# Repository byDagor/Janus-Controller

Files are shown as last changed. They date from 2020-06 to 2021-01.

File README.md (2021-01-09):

# Janus Controller 20.01

The Janus Controller is a Brushless motor driver with an on-board magnetic encoder, a three-phase MOSFET driver, three MOSFET half-bridges, a temperature sensor and current sensing resistors. 

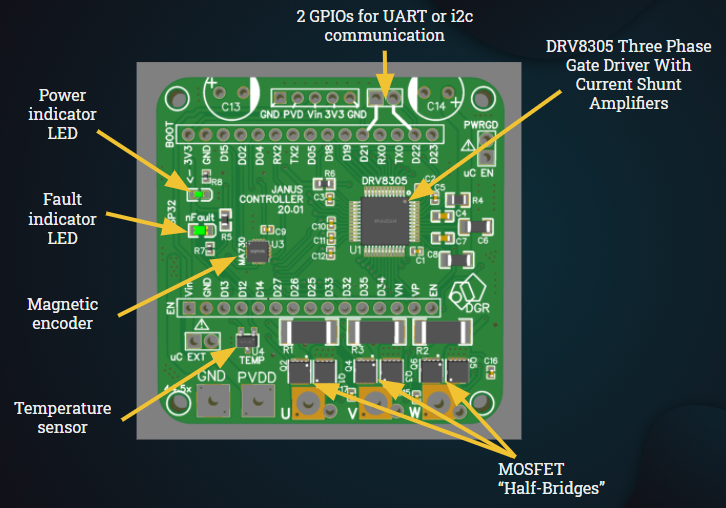
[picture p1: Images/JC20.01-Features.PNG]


Janus Controller was designed to work with the ESP32 Dev-Kit1 as a shield so that the programing of the board is easier for hobbyist and students, and to bring down the overall price of the board.
This board can be used to drive brushless motors as an open-loop system or use the on-board encoder to drive the motors as a closed-loop system and use more complicated algorithms, such as Field Oriented Control for position and velocity control.
I recommend using the [Simple FOC](https://github.com/askuric/Arduino-FOC) Arduino library as it has shown to work perfectly for position and velocity control and is easily implementable, but you can always use your own algorithm. My [example code](JC01F05/JC01F05.ino) uses the [Simple FOC](https://github.com/askuric/Arduino-FOC) library adapted to work with an ESP32.

## Key specs
| Specification | Rating |
| --- |:---:|
| Dimensions | 51 x 51mm |
| Power source voltage | 5-12V |
| Maximum continuous current | Depends on cooling |
| Maximum peak current  | up to 23A |
| Encoder resolution | 4096 cpr/ 0.088 degrees |
| Temperature sensor range | -10 ~ 120°C |

## Getting started

### The board
In this repository you can find everything you need to get you started with your personal projects. The board was designed around the [JLCPCB SMT Parts Library](https://jlcpcb.com/parts), so you should be able to order an SMD assembled board directly from them for a low price. 
You can order this board from your preferred manufacturer, you just need to download the [gerber files](Gerber) and the [SMD BOM](BOM_JC20.01.csv). If you don't order your board from JLCPCB you should make sure that the manufacturer has in stock the needed SMD parts, if not it shouldn't be too difficult to find a replacement (except for the DRV8305 and the MA730).
Furthermore, if you wish to design your own board the [schematic](Schematic) can be a great place to start.  

After receiving the SMD assembled board you need to solder two 470 uF electrolytic capacitors, a few male/ female pins and a voltage source connector. The pins and the connector are optional, but I highly recommend using female header pins for the ESP32 Dev-kit.
The video bellow shows what is needed to prepare the board and how to do it. Alternatively, you can find the needed components in the [*though-hole* BOM](BOM).
<a href="http://www.youtube.com/watch?feature=player_embedded&v=tti3y8_cQ4o
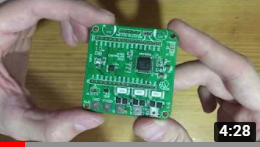
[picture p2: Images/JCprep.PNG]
IMAGE ALT TEXT HERE
" target="_blank"></a>

### ESP32 DEVKIT
As stated before, the Janus Controller was designed as a *shield* for the ESP32 DEVKIT V1. There are a few different ESP32 Devkits out there, make sure the one you buy has the same PIN layout as the Janus Controller.

## Set-up

### The three-phase gate driver
The DRV8305 is a three-phase gate driver that can drive high and low-side N-channel MOSFETS. What makes this driver special is the bunch of programable functions and the protection included.
With the Janus Controller you can use the DRV8305 in its three operation modes: 6-PWM input, 3-PWM input or 1-PWM input. The [example code](JC01F05/JC01F05.ino) works with the driver set through SPI to operate in the 3-PWM mode.
One feature I like is its fault diagnostics, if the nFault pin pulses it means there is a *warning* that can be read through SPI. If the pin is pulled low it means the driver detected a *fault*, which can also be read through SPI, and the output MOSFETs will be placed in their high impedance state.
The Janus Controller board has a red indicator LED that will turn on if a *warning* or a *fault* is detected.
A few of the faults that the driver reports are the following: high temperature flags, source under or over-voltage, VDS over current monitors, gate drive fault, etc.
The picture bellow shows the simplified schematic of the driver that can be found in the [DRV8305 datasheet](https://www.ti.com/lit/ds/symlink/drv8305.pdf?ts=1593641896221&ref_url=https%253A%252F%252Fwww.google.com%252F). Please refer to it if you want to learn more about all the features of this driver IC.
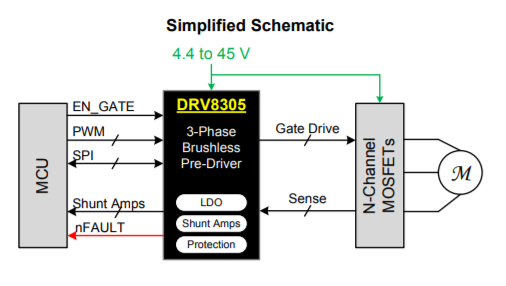
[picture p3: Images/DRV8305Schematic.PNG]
DRV8305
 

### The on-board encoder
The MA730 Magnetic Encoder works with a diametrically polarized magnet, these can be hard to find but you should be able to find a couple options from eBay. 
The [MA730 datasheet](https://www.monolithicpower.com/en/documentview/productdocument/index/version/2/document_type/Datasheet/lang/en/sku/MA730/document_id/3563) recommends a Neodymium alloy (N35) cylinder with dimensions Ø5x3mm inserted into an aluminum shaft, as shown in the picture bellow, placed around 1.5mm above the encoder IC. 
You can use a solid cylindrical magnet of different dimensions without the aluminum shaft and still get excellent results.  

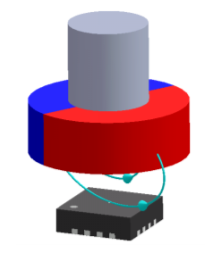
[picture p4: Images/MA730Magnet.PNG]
Magnet
   
The Janus Controller can read the 12-bit ABZ quadrature pins of the encoder to find the position of the rotor. Additionally, a PWM signal can be read to find the absolute position of the rotor (this hasn't been implemented in example code at the moment). 

### External encoder
If you don't want to use the on-board encoder, Janus Controller has access to two GPIOs of the ESP32. These pins can be used to use an external quadrature encoder that should be conected as shown in the picture. Read your encoder's datasheet and check if it needs pull-ups, if so you should be able to use the ESP32's internal pull-ups.
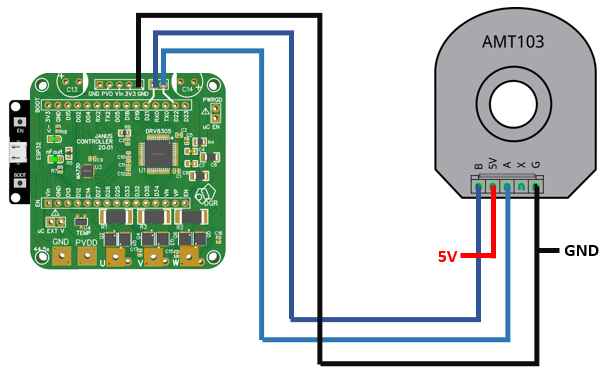
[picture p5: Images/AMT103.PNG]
External encoder


## The example code
The example code was done in the Arduino IDE, running the [Simple FOC](https://github.com/askuric/Arduino-FOC) Arduino Library. By changing a simple parameter, this code allows you to control position and velocity of your burshless motor, or setting a voltage as you would do with a DC motor. 
Make sure you follow the following steps to make sure the code will compile.

### 1. ESP32 set-up
*Random nerd tutorials* have a really easy to follow guide on how to set-up the ESP32 on the Arduino IDE. Follow the steps on [this link](https://randomnerdtutorials.com/installing-the-esp32-board-in-arduino-ide-windows-instructions/) and make sure you can compile one of the examples shown.

### 2. Running the encoder example
Download the [Encoder Tester](JC01F05/JC01F05.ino) and open it on your Arduino IDE. Upload it to the ESP32 and open the Serial terminal and make sure the measurement is accurate. Move the motor's rotor one whole whole rotation and make sure the trerminal prints 360 degrees. 

### 3. Simple FOC library installation
The [Simple FOC](https://github.com/askuric/Arduino-FOC) repository has an extremely detailed explanation on how to install the library. The easiest way is to install it through the library manager as shown in the picture.  
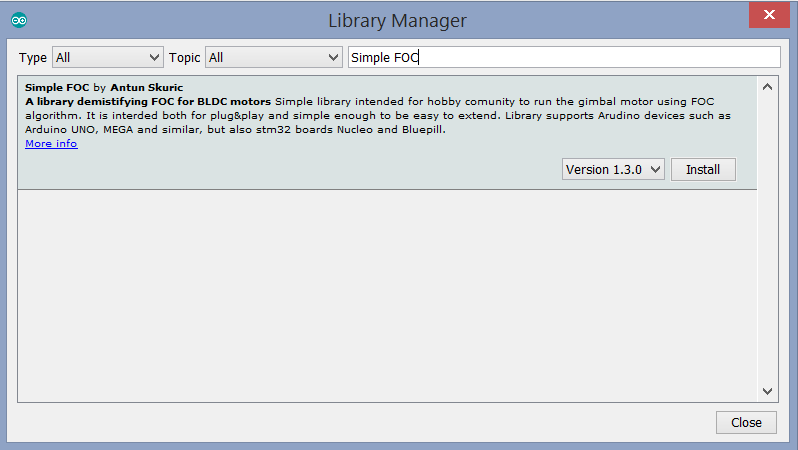
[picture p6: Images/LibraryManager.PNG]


### 4. Running the position control example
Download the [position control example code](JC01F05/JC01F05.ino) and open it on your Arduino IDE; there are a few parameters that you might have to tweak. I really recommend reading the [Simple FOC](https://github.com/askuric/Arduino-FOC) documentation. 

## Brushless motor selection
There are a few general rules that should help you choose the best brushless motor for your particular application. For instance, if you want to build a robot arm, a gimbal, or something that needs relative high torque you should get a low KV motor (usually bellow 300 is good) with a big radius in relation to its length. 
Usually, outrunner brushless motors have more poles than their counterpart, the inrunner, so they spin slower and produce more torque. This makes an outrunner the better choice for this type of application. 
We can use the torque equation of a brushless motor to calculate the ideal torque a motor will produce at a given voltage/ current. The value calculated with this formula will not be the real value because motors are far from ideal. I've found that considering a motor efficiency of around 80% should be good enough for estimating the maximum torque of a brushless motor.
TorqueFormula  \
If you're not sure how much current the motor will draw you can substitute de current in the formula for voltage over the internal resistance of the motor, as show in the equation (2). 
If the internal resistance of the motor seems too low, there is a parameter in the [example code](JC01F05/JC01F05.ino) that restricts the voltage applied to the motor. Generally, a resistance of around 10 ohms should be perfect.  
TorqueFormula2  

## Test Station
The test station is a 3D printed base that holds together the Janus Controller board and a brushless motor with a diametrically polarized magnet. This magnet is attached to the rotor of the motor and placed above the magnetic encoder; around 1.5mm above the encoder is optimal, making sure the center of the magnet is aligned with the center of the encoder.
In the [CAD](CAD) section you can find the CAD for the Test Station, the Janus Controller board, the motor used, the magnet used and the ESP32 Dev-kit. The CAD of the Janus Controller should help you design your own fixture to hold the board near your motor. 

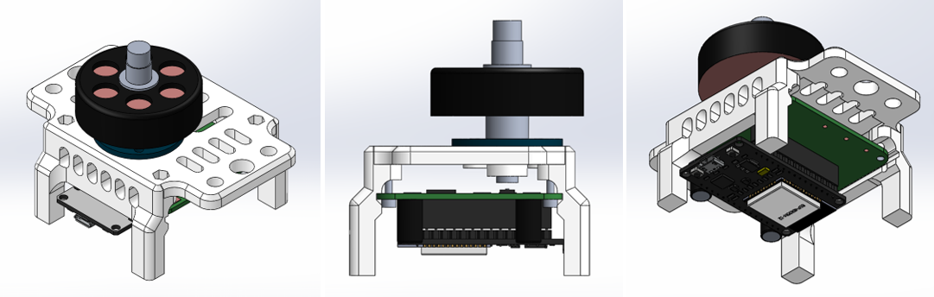
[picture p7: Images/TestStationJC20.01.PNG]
TestStation


## Practical Example
Big J is a five-bar parallel robot that uses direct drive brushless motors as actuators working with two Janus Controllers in position control mode and a master ESP32. Click the image bellow to watch a demo YouTube video.

<a href="http://www.youtube.com/watch?feature=player_embedded&v=JJa_QzbcREA
" target="_blank">IMAGE ALT TEXT HERE</a>

## Contact
I'm happy to hear from your projects and to help in any way possible!  
davidglzrys@gmail.com  
[Linkedin](https://www.linkedin.com/in/david-g-reyes/)  
[YouTube](https://www.youtube.com/channel/UC4gsPZan2T4v5LpJ5J_t7sQ/featured)

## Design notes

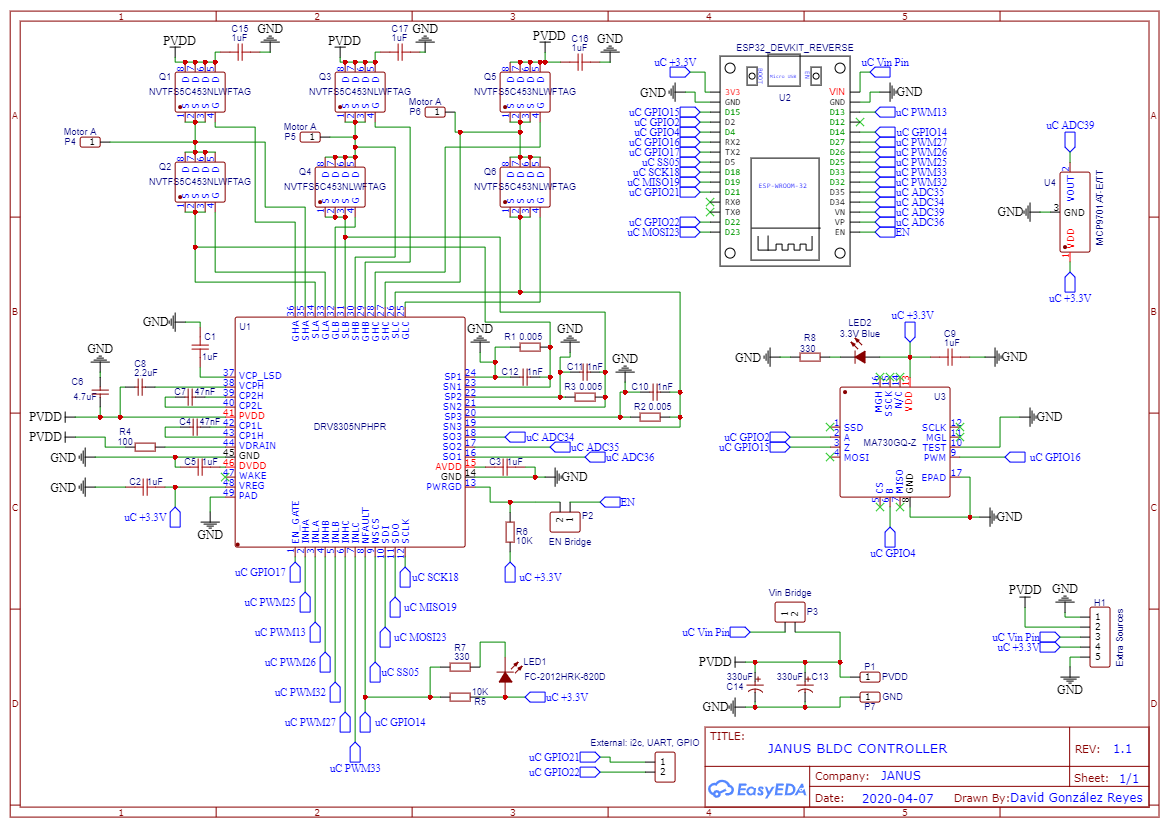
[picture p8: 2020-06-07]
JC20.01/Schematics/JanusController20.01_Schematics.png

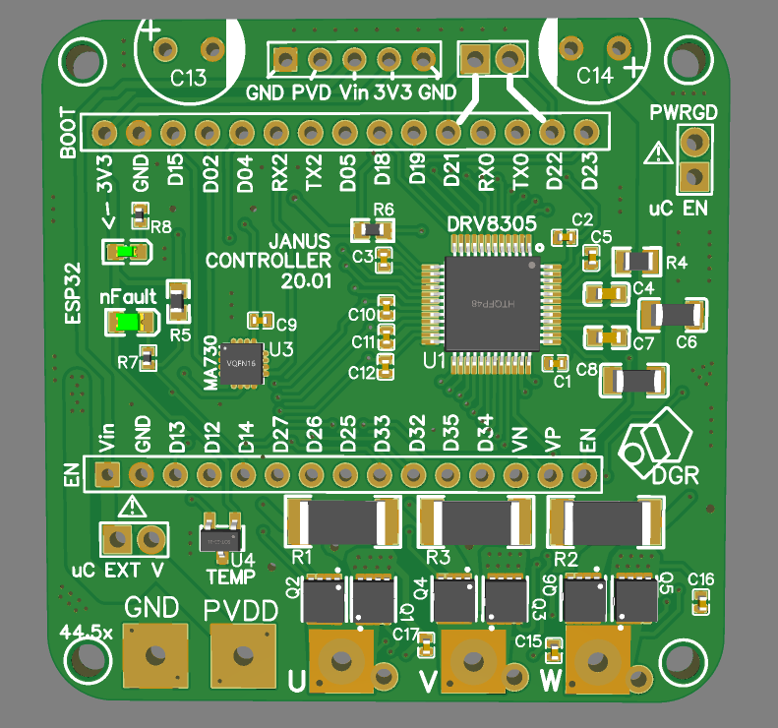
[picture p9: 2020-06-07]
JC20.01/Images/RenderFront20.01.PNG

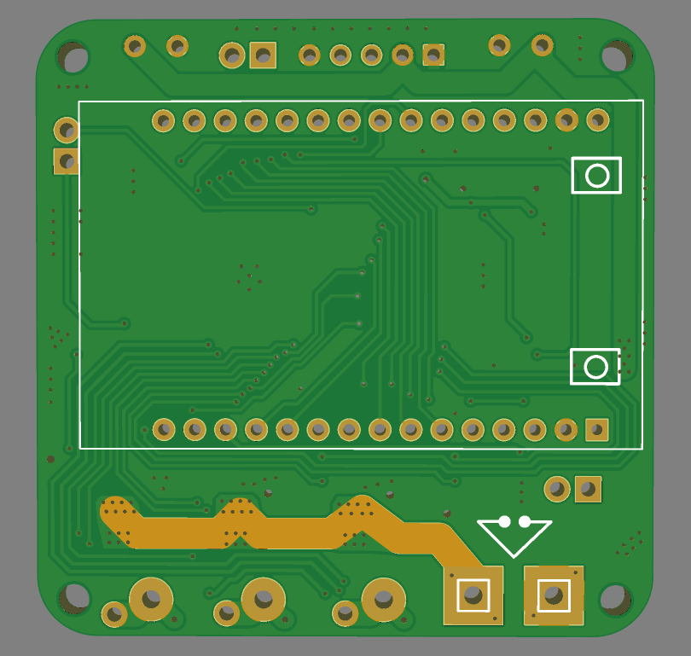
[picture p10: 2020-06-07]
JC20.01/Images/RenderBack20.01.PNG

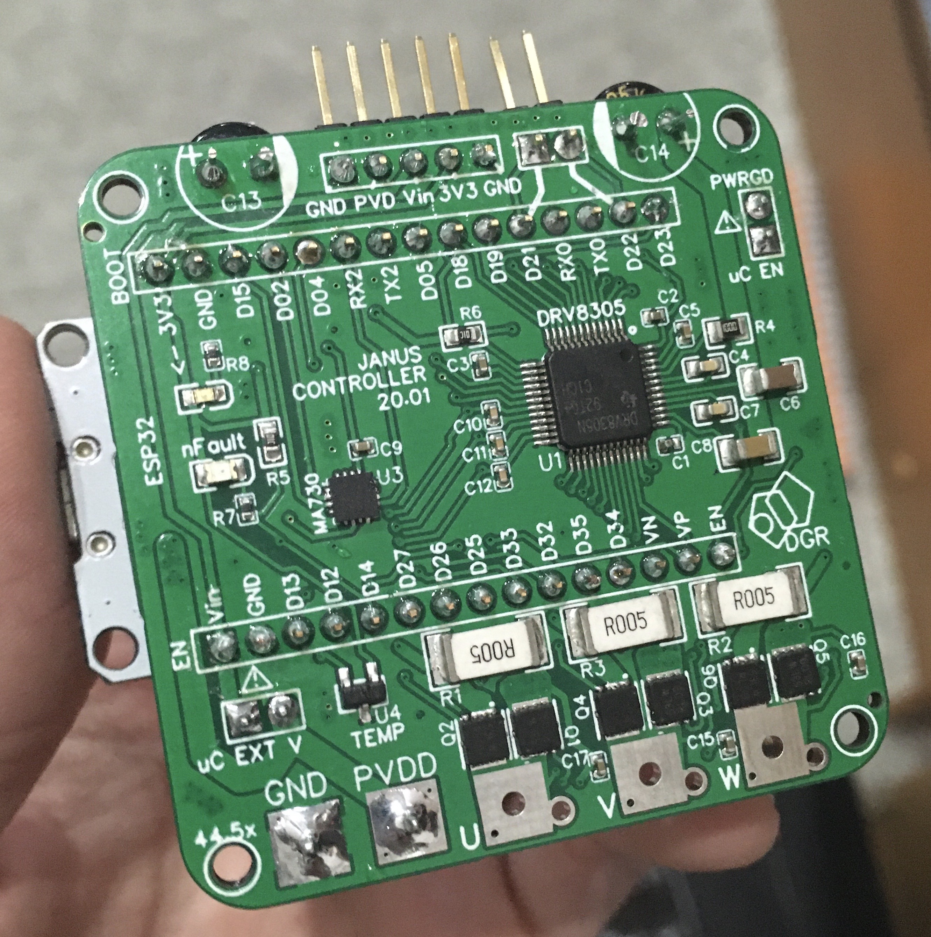
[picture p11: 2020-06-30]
JC20.01/Images/Front20.01.JPG

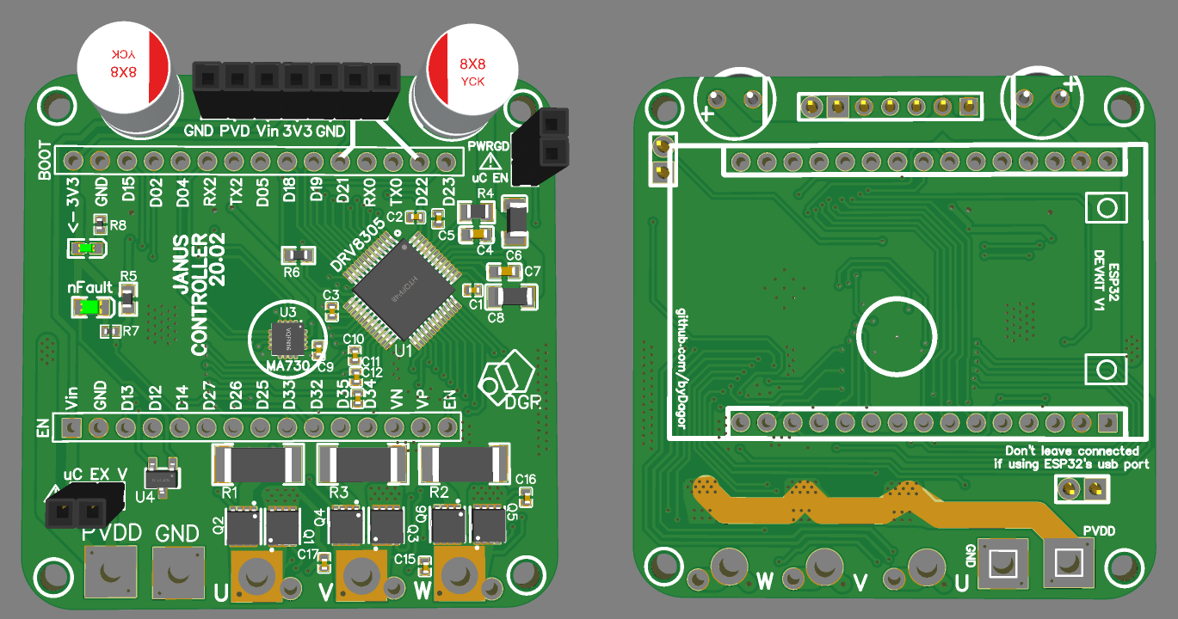
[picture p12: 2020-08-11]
Images/JC20.02.png

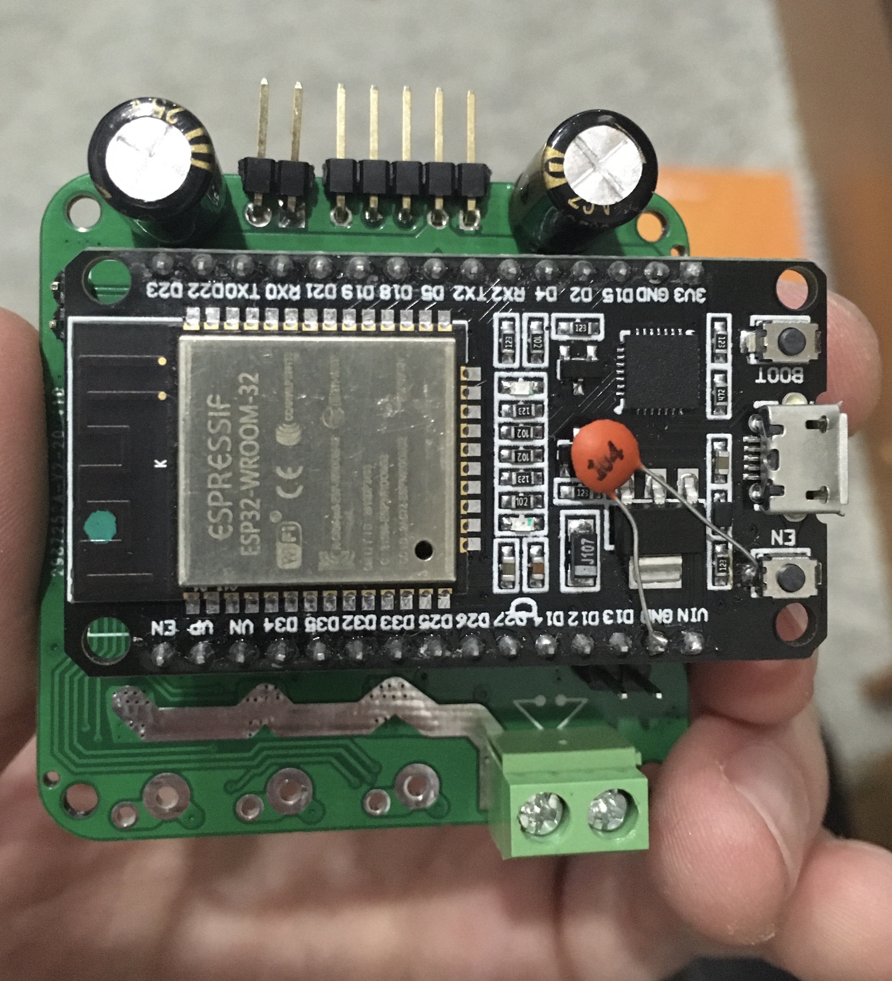
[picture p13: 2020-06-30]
JC20.01/Images/Back20.01.JPG

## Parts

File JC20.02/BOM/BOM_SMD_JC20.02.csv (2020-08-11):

ID | Name | Designator | Footprint | Quantity | Manufacturer Part | Manufacturer | Supplier | Supplier Part | LCSC Assembly
1 | 2.2uF | C8 | C1206 | 1 | CL31B225KBHNNNE | SAMSUNG | LCSC | C50254 | Yes
2 | 10uF | C18,C19 | C0805 | 2 | CL21A106KAYNNNE | SAMSUNG | LCSC | C15850 | Yes
3 | 100 | R4 | R0805 | 1 | 0805W8F1000T5E | UniOhm | LCSC | C17408 | Yes
4 | MCP9701AT-E/TT | U4 | SOT-23-3_L3.0-W1.7-P0.95-LS2.9-BR | 1 | MCP9701AT-E/TT | Microchip Tech | LCSC | C150830 | Yes
5 | FC-2012HRK-620D | LED1 | LED0805-RD | 1 | FC-2012HRK-620D | NATIONSTAR | LCSC | C84256 | Yes
6 | 330 | R7,R8 | R0402 | 2 | 0402WGF3300TCE | UniOhm | LCSC | C25104 | Yes
7 | NVTFS5C453NLWFTAG | Q1,Q3,Q5,Q6,Q4,Q2 | POWERTDFN-8_L3.1-W3.1-P0.65-LS3.3-BL | 6 | NVTFS5C453NLWFTAG | ON | LCSC | C145551 | Yes
8 | MA730GQ-Z | U3 | VQFN-16_L3.0-W3.0-P0.50-TL-EP | 1 | MA730GQ-Z | Monolithic Power Systems | LCSC | C161798 | Yes
9 | 1nF | C10,C11,C12 | C0402 | 3 | 0402B102K500NT | FH | LCSC | C1523 | Yes
10 | 3.3V Blue | LED2 | LED0603-R-RD | 1 | 19-217/BHC-ZL1M2RY/3T | EVERLIGHT | LCSC | C72041 | Yes
11 | 0.005 | R2,R1,R3 | R2512 W/ KELVIN | 3 | MS122WJ050MT4E | UniOhm | LCSC | C49483 | Yes
12 | 4.7uF | C6 | C1206 | 1 | 1206B475K500NT | FH | LCSC | C29823 | Yes
13 | 10K | R5,R6 | R0603 | 2 | 0603WAF1002T5E | UniOhm | LCSC | C25804 | Yes
14 | 1uF | C5,C2,C1,C3,C9,C15,C16,C17 | C0402 | 8 | CL05A105KA5NQNC | SAMSUNG | LCSC | C52923 | Yes
15 | DRV8305NPHPR | U1 | HTQFP-48_L7.0-W7.0-P0.50-LS9.0-BL-EP | 1 | DRV8305NPHPR | Texas Instruments | LCSC | C75602 | Yes
16 | 47nF | C7,C4 | C0603 | 2 | CL10B473KB8NNNC | SAMSUNG | LCSC | C1622 | Yes

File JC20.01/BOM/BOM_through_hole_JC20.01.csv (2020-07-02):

ID | Name | Designator | Quantity
16 | 25V 470 uF Electrolytic Capacitor | C13,C14 | 2
17 | Femal pins |  | 30
18 | Male pins |  | 11
19 | Pin jumper |  | 2
20 | ESP32 DEVKIT |  | 1
21 | 2-pin screw terminal |  | 1

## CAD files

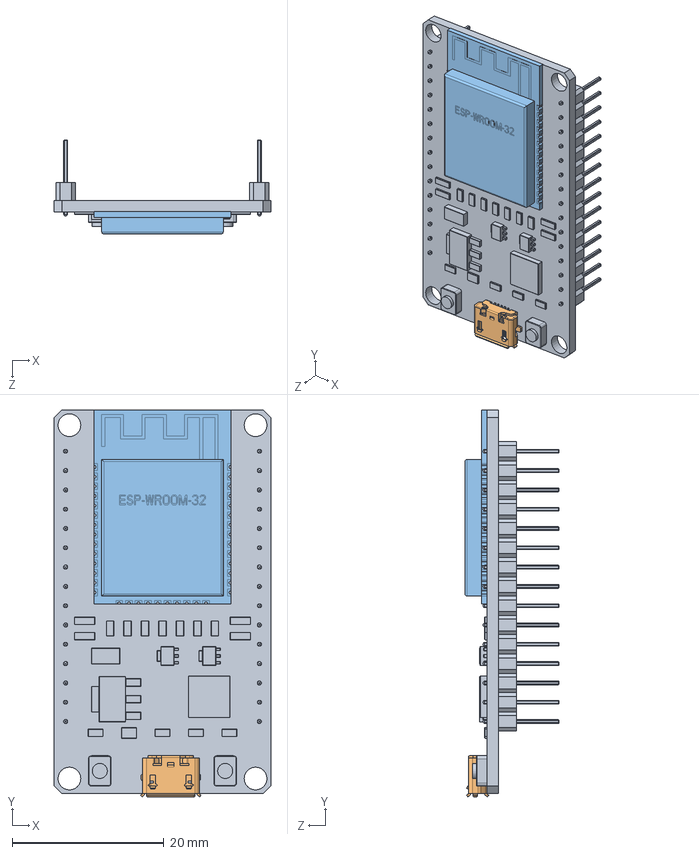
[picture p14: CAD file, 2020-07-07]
JC20.01/CAD/ESP32_DevKit1.SLDASM
28.5 x 50.9 x 12.4 mm
6.ESP-32
Micro_USB
ESP-WROOM-32

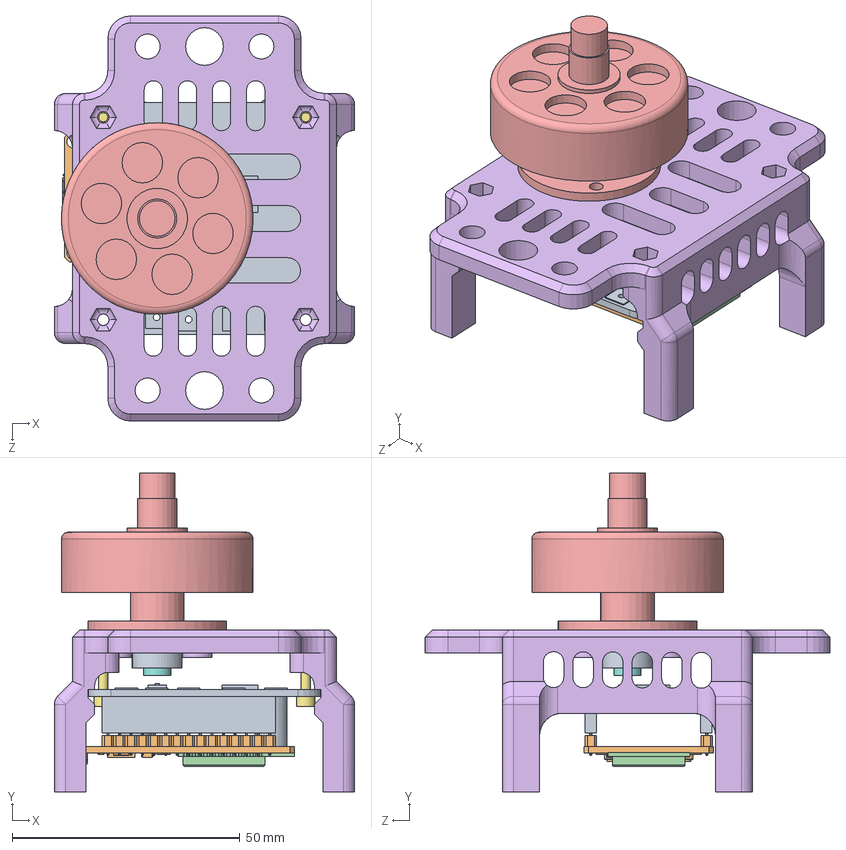
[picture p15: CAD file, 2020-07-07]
JC20.01/CAD/Test Station JC20.01.SLDASM
66.0 x 70.1 x 89.0 mm
PCB Janus Controller 20.01
6.ESP-32
Micro_USB
ESP-WROOM-32
YUNEEC YUMN4234 B
Test Station Base 012
Screw 2.5mm x 10mm x 2
Diametrical Magnet 6x6mm
Magnet Joint 012

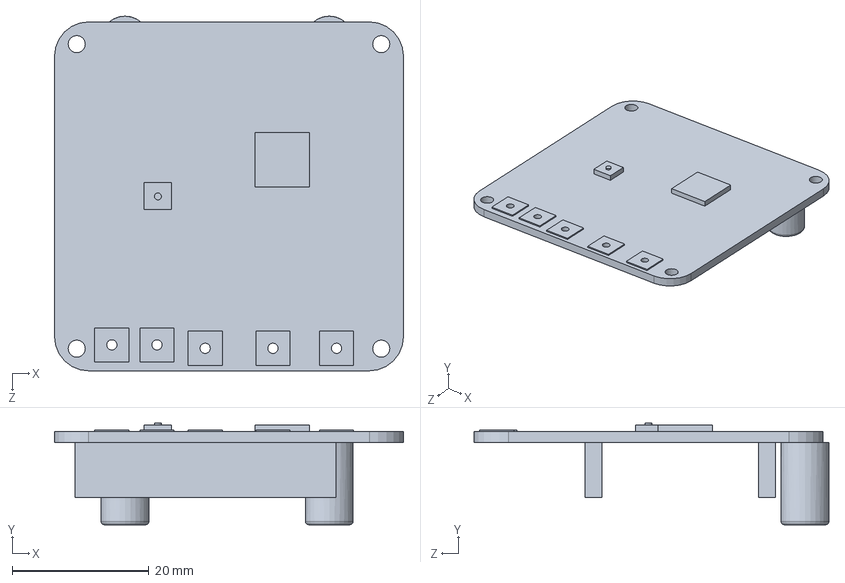
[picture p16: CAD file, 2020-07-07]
JC20.01/CAD/PCB Janus Controller 20.01.SLDPRT
51.0 x 14.9 x 51.8 mm

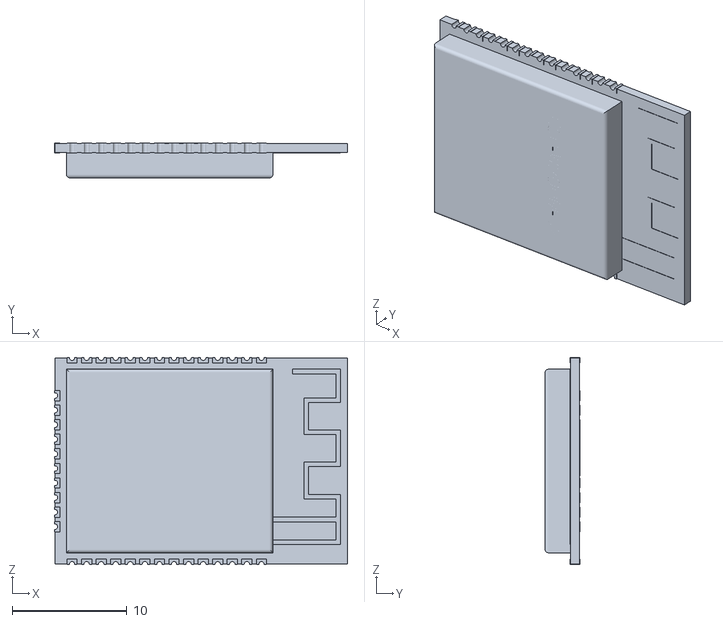
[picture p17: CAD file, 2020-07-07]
JC20.01/CAD/STL/Test Station JC20.01 - ESP32_DevKit1-1 ESP-WROOM-32-1.STL
25.5 x 3.04 x 18.1

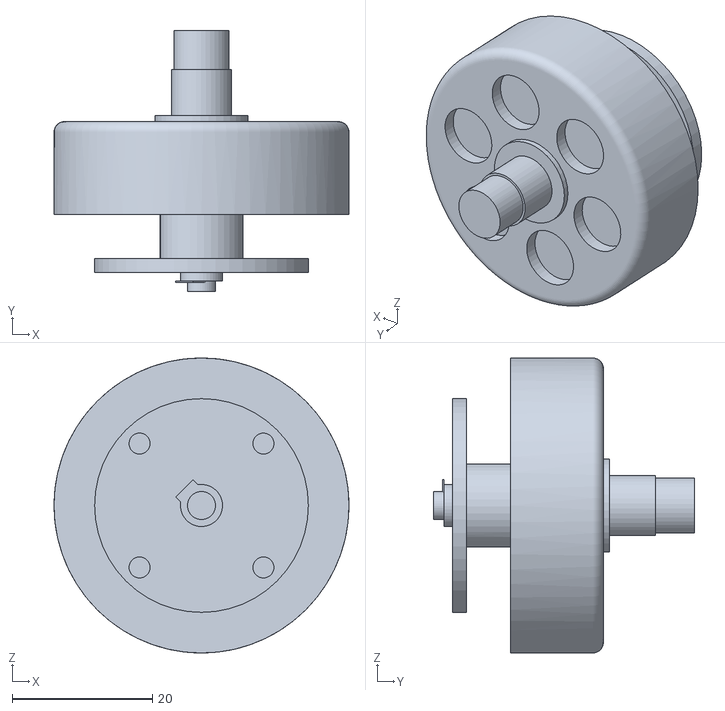
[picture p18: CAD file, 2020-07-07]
JC20.01/CAD/STL/Test Station JC20.01 - YUNEEC YUMN4234 B-1.STL
42.1 x 37.2 x 42.1

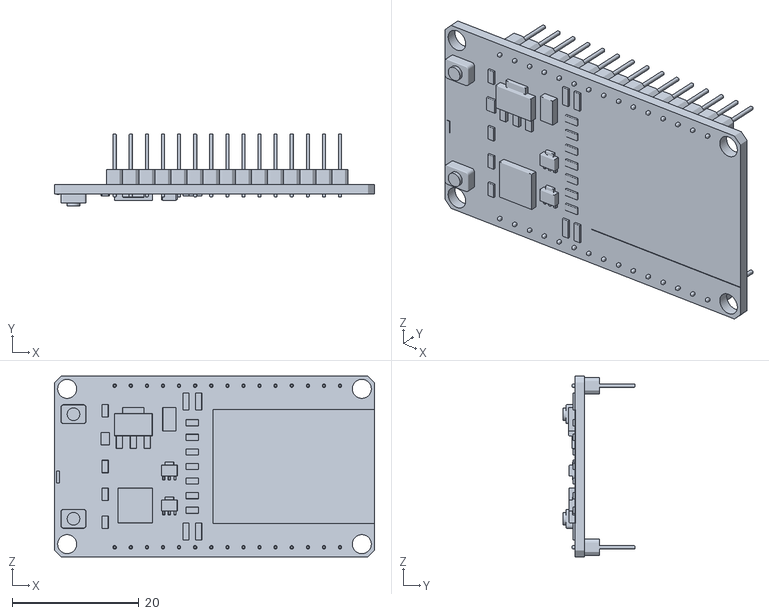
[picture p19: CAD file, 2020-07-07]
JC20.01/CAD/STL/Test Station JC20.01 - ESP32_DevKit1-1 6.ESP-32-1.STL
50.5 x 11.4 x 28.5

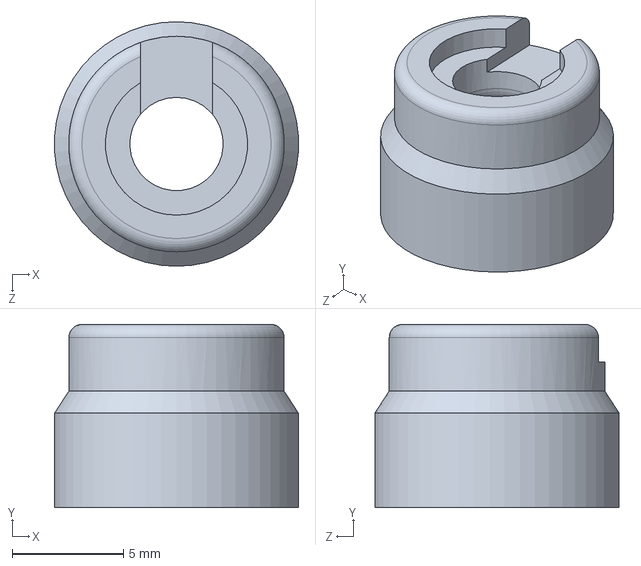
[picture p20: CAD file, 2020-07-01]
JC20.01/CAD/Magnet Joint 012.SLDPRT
11.0 x 8.25 x 11.0 mm

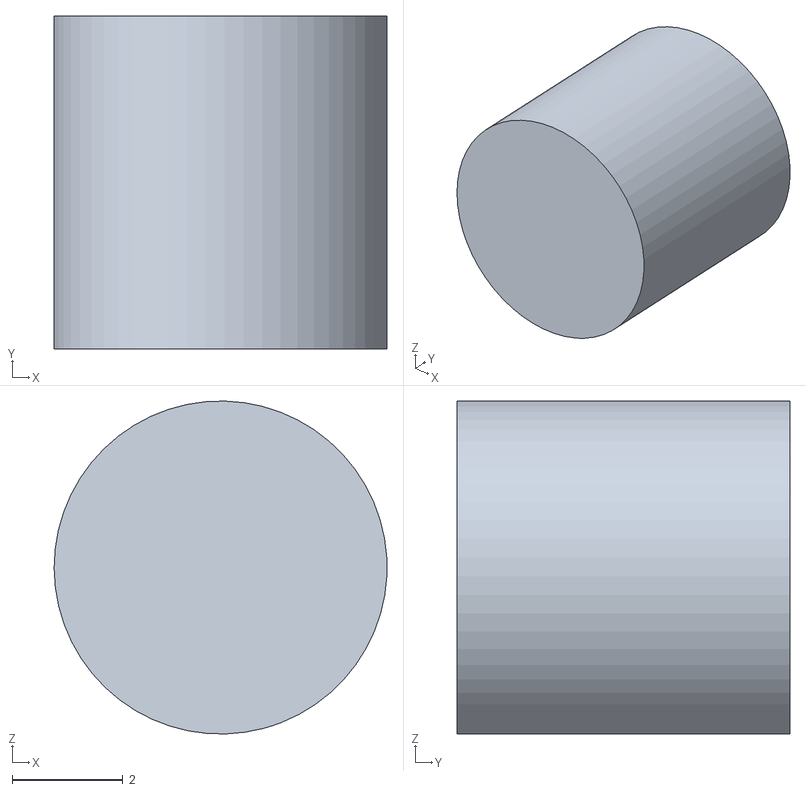
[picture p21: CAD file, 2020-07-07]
JC20.01/CAD/STL/Test Station JC20.01 - Diametrical Magnet 6x6mm-1.STL
6.00 x 6.00 x 6.00

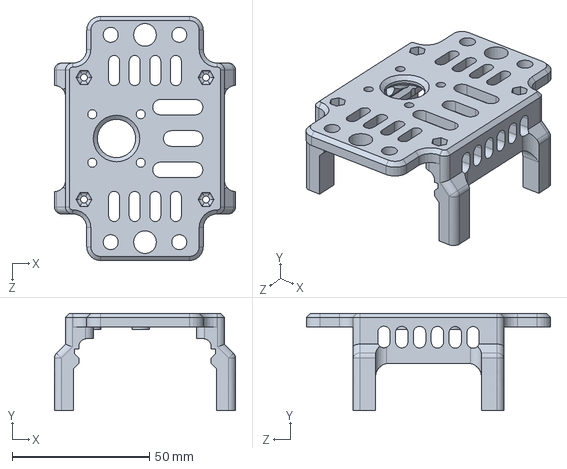
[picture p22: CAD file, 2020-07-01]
JC20.01/CAD/Test Station Base 012.SLDPRT
66.0 x 35.6 x 89.0 mm

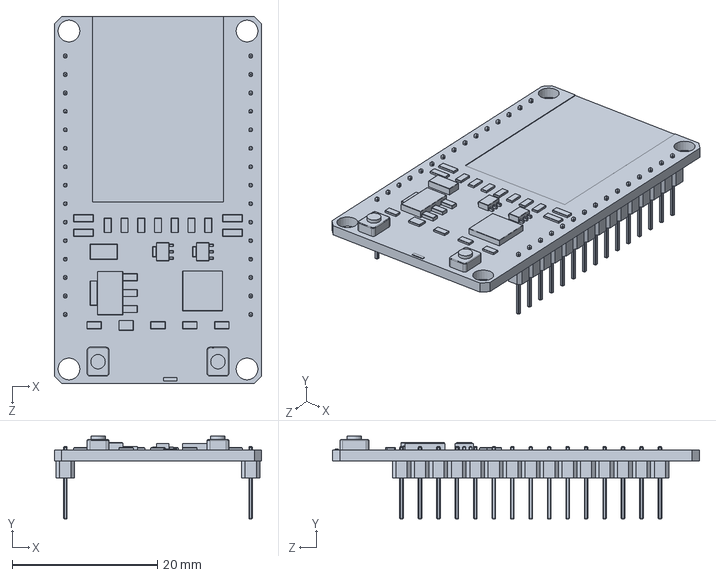
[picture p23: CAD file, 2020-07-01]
JC20.01/CAD/6.ESP-32.SLDPRT
28.5 x 11.4 x 50.5 mm

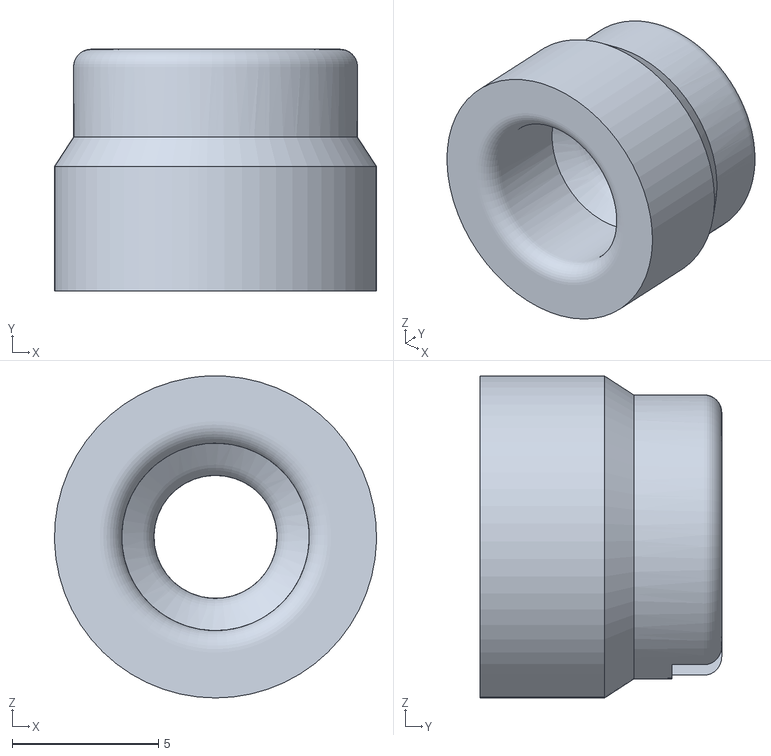
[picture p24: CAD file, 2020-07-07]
JC20.01/CAD/STL/Test Station JC20.01 - Magnet Joint 012-1.STL
11.0 x 8.25 x 11.0

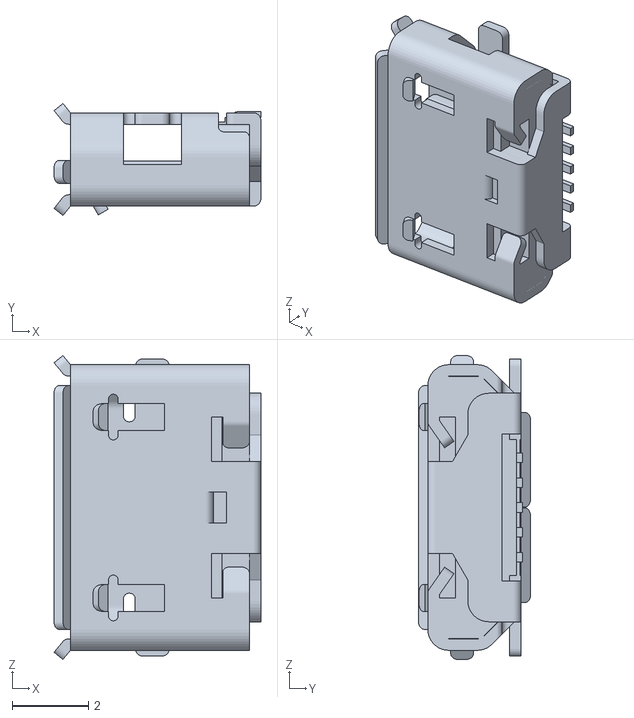
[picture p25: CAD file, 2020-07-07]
JC20.01/CAD/STL/Test Station JC20.01 - ESP32_DevKit1-1 Micro_USB-1.STL
5.43 x 2.94 x 7.98

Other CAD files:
JC20.01/CAD/STL/ESP32_DevKit1 - ESP-WROOM-32-1.STL
JC20.01/CAD/Diametrical Magnet 6x6mm.SLDPRT
JC20.01/CAD/STL/Test Station JC20.01 - PCB Janus Controller 20.01-1.STL
JC20.01/CAD/YUNEEC YUMN4234 B.SLDPRT
JC20.01/CAD/ESP-WROOM-32.sldprt
JC20.01/CAD/STL/Micro_USB.STL
JC20.01/CAD/STL/6.ESP-32.STL
JC20.01/CAD/STL/Diametrical Magnet 6x6mm.STL
JC20.01/CAD/STL/ESP-WROOM-32.STL
JC20.01/CAD/STL/ESP32_DevKit1 - 6.ESP-32-1.STL
JC20.01/CAD/STL/ESP32_DevKit1 - Micro_USB-1.STL
JC20.01/CAD/STL/Magnet Joint 012.STL
JC20.01/CAD/STL/PCB Janus Controller 20.01.STL
JC20.01/CAD/STL/Test Station Base 012.STL
JC20.01/CAD/STL/Test Station JC20.01 - Screw 2.5mm x 10mm-1.STL
JC20.01/CAD/STL/Test Station JC20.01 - Screw 2.5mm x 10mm-2.STL
JC20.01/CAD/STL/Test Station JC20.01 - Test Station Base 012-2.STL
JC20.01/CAD/STL/YUNEEC YUMN4234 B.STL
JC20.01/CAD/Screw 2.5mm x 10mm.SLDPRT

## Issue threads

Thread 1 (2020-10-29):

About the second drive board

zhuangfengzi, 2020-10-29:
Very interested in this driver board! The author did a great job!

I made a couple of second versions, and in the test, I uploaded encoder_ Test code, but ma730 doesn't work. Is ma730 broken? In the first edition, I saw that you welded a capacitor on the en and GND ends of the esp32 board. Is this necessary?

There is also the problem of drv8305. I still don't know. Can you share the relevant learning materials?

Ask the author to help answer? Thank you very much!

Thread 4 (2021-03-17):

ESP32 Code

xpeedster, 2021-03-17:
Hi, I am working on a project where I need to contorl a motor using DRV8305. I've been looking into the datasheet of the driver and there are some registers that must be written to before moving the motor. however, I am not able to move the motor. Maybe I am doing something wrong in that process. Could you share the code?

Thanks for your help.

xpeedster, 2021-03-17:
By the way, you may have not noticed, the "example code" link in the Readme does not work.

Blimpyway, 2021-03-17:
You mean [this?](https://github.com/byDagor/Dagor-Brushless-Controller/tree/master/Firmware/a_DA024F011)

byDagor, 2021-07-21:
The code example for SimpleFOC is outdated, the library has changed since. The code relating configuring the DRV8305 still works and is also what I use in the Dagor Controller.

artayasa, 2024-04-22:
> The code example for SimpleFOC is outdated, the library has changed since. The code relating configuring the DRV8305 still works and is also what I use in the Dagor Controller.

Hi mate it posible change the drv wirh own driver mosfet like ir2101 and mosfet?? Only SPI not use? It posible?

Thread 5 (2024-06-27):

JLC website has changed, so BOM and pick and place files need to change...

eduardkieser, 2024-06-27:
Hello @byDagor. First of all, thank you so much for doing this it looks really cool.
Thank you. thank you. thank you.

I tried to order some Janus Controllers from JLC pcb but it seems that the website has changed and required the BOM and pick and place files to be in a different format.

I know ki-cad now has a plugin that allows you to generate all the manufacturing files for JLC PCB in the new style. I'm sure whatever tool you are using might have the same feature.

If there is a way that I can help you with this please let me know.

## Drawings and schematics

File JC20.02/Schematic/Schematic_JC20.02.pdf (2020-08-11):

# ESP-WROOM-32 BOOT EN

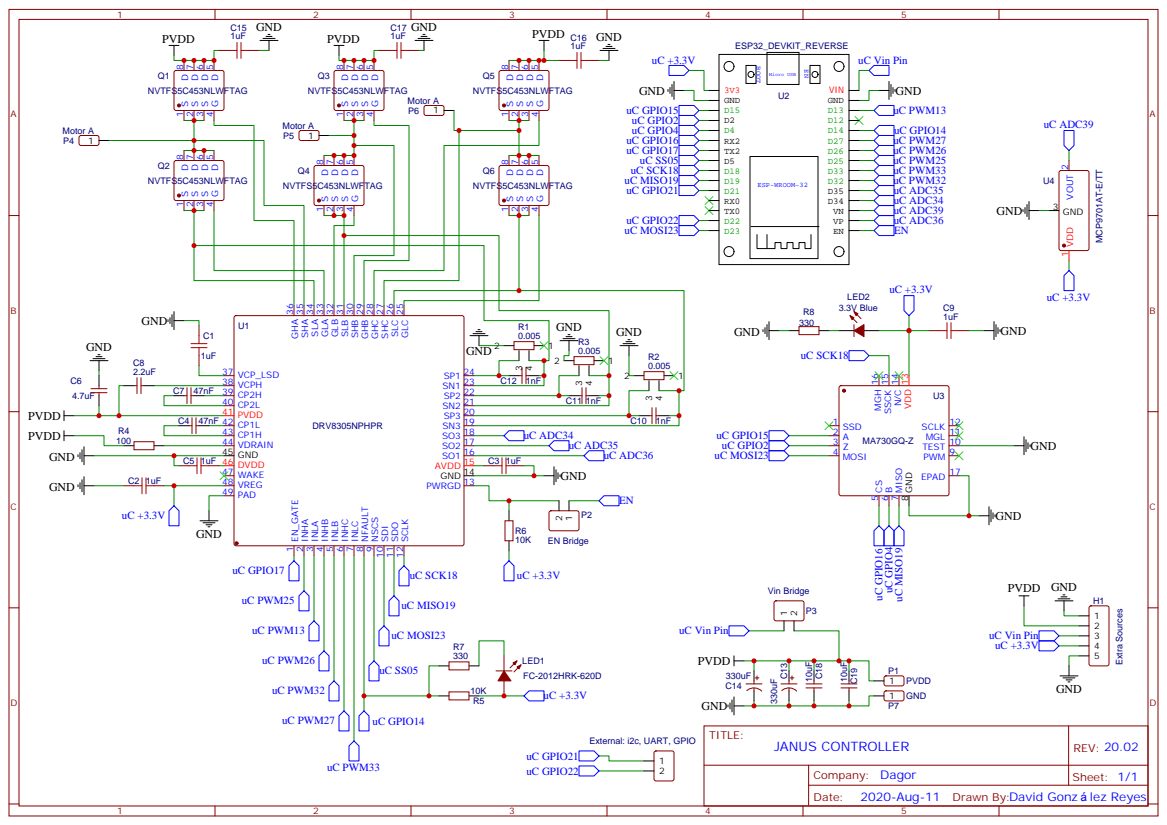
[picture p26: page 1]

GLC 25 SLC 26 SHC 27 GHC 28 GHB 29 SHB 30 SLB 31 GLB 32 GLA 33 SLA 34 SHA 35 GHA 36
PWRGD 13 GND 14 AVDD 15 SO1 16 SO2 17 SO3 18 SN3 19 SP3 20 SN2 21 SP2 22 SN1 23 SP1 24

Drawn By:David Gonz lez Reyes

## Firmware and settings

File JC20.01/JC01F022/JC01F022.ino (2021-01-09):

//Janus Brushless Controller Firmware 022 (Includes current sensing)

//SimpleFOC Version 2.0.1
#include <SimpleFOC.h>
#include <SPI.h>
#include "driver/mcpwm.h"
#include "soc/mcpwm_reg.h"
#include "soc/mcpwm_struct.h"

//#######_USER VARIABLES_#######
byte pp = 7;                  //BLDC motor number of pole pairs
float phaseRes = 0.560;       //Phase winding resistance [ohms]
byte sourceVoltage = 12;      //Voltage of your power source [Volts]
byte maxCurrent = 2;          //Rough approximation of max current [Amps]

//#######_CONTROLLER PARAMETERS_#######
float ki = 0.002;             //Velocity control loop PROPORTIONAL gain value
float ti = 2.5;               //Velocity control loop INTEGRAL gain value
float lpFilter = 0.000;
float kp = 10;                //Position control loop PROPORTIONAL gain value
float voltageRamp = 25;       //Change in voltage allowed [Volts per sec]
float voltageLimit = phaseRes*maxCurrent;
float velocityLimit = 2000;   //Velocity limit [rpm]
 
//#######_DRV8305_########
//Datasheet: www.ti.com/lit/ds/symlink/drv8305.pdf
#define enGate 17       //Chip Enable
#define nFault 14       //Fault reading
#define cs 5           //DRV8305 Chip-select
#define so1 36
#define so2 35
#define so3 34
bool faultTrig = false;

//####_CURRENT READING_####
/*
static mcpwm_dev_t *MCPWM[2] = {&MCPWM0, &MCPWM1};
static portMUX_TYPE mcpwm_spinlock = portMUX_INITIALIZER_UNLOCKED;
int a1, a2, a3;         //Current readings from internal current sensor amplifiers
static void IRAM_ATTR isr_handler(void*);
byte currentState = 1;
*/

//######_MA730_######
//A and B encoder inputs
#define Int1 4             // interrupt 0
#define Int2 2             // interrupt 1

//######_TEMPERATURE SENSOR_######
#define vTemp 39
byte maxTemp = 80;      //Maximum temperature [°C]
float temp;

//#####_TIME MANAGEMENT_#####
float runTime, prevT = 0, timeDif, stateT;
int timeInterval = 1000, totalTempTime;

//####_SIMPLEFOC INSTANCES_####
BLDCMotor motor = BLDCMotor(pp);   //BLDCMotor instance
BLDCDriver3PWM driver = BLDCDriver3PWM(25, 26, 27);     //3PWM Driver instance
Encoder sensor = Encoder(Int1, Int2, 1024);       // Quadrature encoder instance

// Interrupt routine intialisation
// channel A and B callbacks
void doA(){sensor.handleA();}
void doB(){sensor.handleB();}

//--------------------------------------------Set-up--------------------------------------------
void setup() {
  Serial.begin(115200);

  //analogSetCycles(2);

  //Pinmodes
  pinMode(so1, INPUT);
  pinMode(so2, INPUT);
  pinMode(so3, INPUT);
  pinMode(nFault, INPUT);
  pinMode(enGate, OUTPUT);
  digitalWrite(enGate, LOW);

  //SPI start up
  pinMode(cs, OUTPUT);
  digitalWrite(cs, HIGH);
  SPI.begin();
  SPI.setBitOrder(MSBFIRST);
  SPI.setDataMode(SPI_MODE1);

  //Motor driver initialization
  delay(250);
  Serial.println("DRV8305 INIT");
  drv_init();
  delay(500);

  Serial.println("enGate Enabled");
  digitalWrite(enGate, HIGH);
  delay(500);

  //Initialise magnetic sensor hardware
  sensor.init();

  //If using encoder
  sensor.enableInterrupts(doA, doB); 
  
  //Link the motor to the sensor
  motor.linkSensor(&sensor);
  
  // driver config, power supply voltage [V]
  driver.voltage_power_supply = sourceVoltage;
  driver.init();
  motor.linkDriver(&driver);

  // set FOC loop to be used: ControlType::voltage, velocity, angle
  motor.controller = ControlType::voltage;

  // Sensor aligning voltage
  motor.voltage_sensor_align = voltageLimit/2;
  
  // velocity PI controller parameters, default K=0.5 Ti = 0.01
  motor.PID_velocity.P = ki;
  motor.PID_velocity.I = ti;
  motor.PID_velocity.D = 0;
  motor.voltage_limit = voltageLimit;
  motor.LPF_velocity.Tf = lpFilter;
  
  // angle P controller, default K=70
  motor.P_angle.P = kp;
  // maximal velocity of the poisition control, default 20
  motor.velocity_limit = velocityLimit;

  motor.useMonitoring(Serial);      // use monitoring functionality
  motor.init();                     // initialise motor
  motor.initFOC();            // align sensor/ encoder and start FOC
  Serial.println("Ready BLDC.");
  
  _delay(1000);
  Serial.println(motor.zero_electric_angle);

  //Current sensing interrupt routines
  /*
  MCPWM[MCPWM_UNIT_0]->int_ena.timer0_tep_int_ena = true;//A PWM timer 0 TEP event will trigger this interrupt
  MCPWM[MCPWM_UNIT_0]->int_ena.timer1_tep_int_ena = true;//A PWM timer 1 TEP event will trigger this interrupt
  MCPWM[MCPWM_UNIT_0]->int_ena.timer2_tep_int_ena = true;//A PWM timer 2 TEP event will trigger this interrupt
  mcpwm_isr_register(MCPWM_UNIT_0, isr_handler, NULL, ESP_INTR_FLAG_IRAM, NULL);  //Set ISR Handler
  */
}

//--------------------------------------------Loop--------------------------------------------
void loop() {
  motor.loopFOC();
  motor.move(); // target set by the motor.command()  - or by variable motor.target

  float e = sensor.getAngle();
  Serial.println(e,4);
  
  motor.command(serialReceiveUserCommand());        //user communication

  //Time managment
  runTime = micros();
  timeDif = runTime - prevT;
  prevT = runTime;
  stateT += timeDif;

  //Functions inside this "if" will execute at a 10hz rate
  if(stateT >= 200000){
    stateT = 0;
    tempStatus();
    faultStatus();
    //Serial.print(temp);
    //Serial.print(", ");
    //Serial.print(a1);
    //Serial.print(", ");
    //Serial.print(a2);
    //Serial.print(", ");
    //Serial.println(a3);
  }
  
}

//Temperature status and manager
void tempStatus(){
  static int tFlag;

  //Read voltage from temperature sensor and transform it to °C
  float vOut = analogRead(vTemp);
  temp = (((vOut*3.3)/4095)-0.4)/0.0195;
  //Serial.println(temp,2);
  
  if (temp >= 80 && tFlag == false){
    int tempTime = micros();
    totalTempTime += tempTime;

    //If temperature is high for 3 seconds disable DRV
    if(totalTempTime >= 3000000){
      tFlag = true;
      digitalWrite(enGate, LOW);
      Serial.print("enGate Disabled - Temperature protection: ");
      Serial.println(temp);
    }
    
  }
  else if (temp <= 80 && tFlag == false){
    totalTempTime = 0;
  }
  
}

//Configure DRV8305 to desired operation mode
void drv_init(){

  //Set to three PWM inputs mode
  digitalWrite(cs, LOW);
  byte resp1 = SPI.transfer(B00111010);
  byte resp2 = SPI.transfer(B10000110);
  digitalWrite(cs, HIGH);

  Serial.println(resp1, BIN);
  Serial.println(resp2, BIN);
  
}

//Fault status and manager for the DRV8305
//Datahseet pages 37 and 38
void faultStatus(){
  //Read nFault pin from DRV8305 - LOW == error / HIGH == normal operation
  int fault = digitalRead(nFault);
  
  if(fault == LOW && faultTrig == false){
    Serial.println("Fault detected");
    faultTrig = true;
    //Check warning and watchdog reset (Address = 0x1)
    digitalWrite(cs, LOW);
    byte ft1 = SPI.transfer(B10001000);
    byte ft2 = SPI.transfer(B00000000);
    digitalWrite(cs, HIGH);
    Serial.println("Address = 0x1");
    Serial.println(ft1,BIN);
    Serial.println(ft2,BIN);

    //Check OV/VDS Faults (Address = 0x2)
    digitalWrite(cs, LOW);
    byte ft3 = SPI.transfer(B10010000);
    byte ft4 = SPI.transfer(B00000000);
    digitalWrite(cs, HIGH);
    Serial.println("Address = 0x2");
    Serial.println(ft3,BIN);
    Serial.println(ft4,BIN);

    //Check IC Faults (Address = 0x3)
    digitalWrite(cs, LOW);
    byte ft5 = SPI.transfer(B10011000);
    byte ft6 = SPI.transfer(B00000000);
    digitalWrite(cs, HIGH);
    Serial.println("Address = 0x3");
    Serial.println(ft5,BIN);
    Serial.println(ft6,BIN);

    //Check VGS Faults (Address = 0x4)
    digitalWrite(cs, LOW);
    byte ft7 = SPI.transfer(B10100000);
    byte ft8 = SPI.transfer(B00000000);
    digitalWrite(cs, HIGH);
    Serial.println("Address = 0x4");
    Serial.println(ft7,BIN);
    Serial.println(ft8,BIN);
  }
}

/*
static void IRAM_ATTR isr_handler(void*){
  uint32_t mcpwm_intr_status_0;
  uint32_t mcpwm_intr_status_1;
  uint32_t mcpwm_intr_status_2;
  mcpwm_intr_status_0 = MCPWM[MCPWM_UNIT_0]->int_st.timer0_tep_int_st;
  mcpwm_intr_status_1 = MCPWM[MCPWM_UNIT_0]->int_st.timer1_tep_int_st;
  mcpwm_intr_status_2 = MCPWM[MCPWM_UNIT_0]->int_st.timer2_tep_int_st;
  if(mcpwm_intr_status_0 > 0 && currentState == 1){
    a1 = analogRead(so1);
    currentState = 2; 
  }
  else if(mcpwm_intr_status_1 > 0 && currentState == 2){
    a2 = analogRead(so2);
    currentState = 3;
  }
  else if(mcpwm_intr_status_2 > 0 && currentState == 3){
    a3 = analogRead(so3);  
    currentState = 1;
  }
  MCPWM[MCPWM_UNIT_0]->int_clr.timer0_tep_int_clr = mcpwm_intr_status_0;
  MCPWM[MCPWM_UNIT_0]->int_clr.timer1_tep_int_clr = mcpwm_intr_status_1;
  MCPWM[MCPWM_UNIT_0]->int_clr.timer2_tep_int_clr = mcpwm_intr_status_2;
}
*/

//Utility function enabling serial communication the user
String serialReceiveUserCommand() {
  // a string to hold incoming data
  static String received_chars;
  String command = "";

  while (Serial.available()) {
    // get the new byte:
    char inChar = (char)Serial.read();
    // add it to the string buffer:
    received_chars += inChar;
    // end of user input
    if (inChar == '\n') {
      // execute the user command
      command = received_chars;
      // reset the command buffer 
      received_chars = "";
    }
  }
  return command;
}

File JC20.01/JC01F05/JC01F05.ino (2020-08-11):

//#####_Libraries_#####
#include <SPI.h>
#include <SimpleFOC.h>
#include "driver/mcpwm.h"
#include "soc/mcpwm_reg.h"
#include "soc/mcpwm_struct.h"

//#######_MCPWM Pins_#######
#define GPIO_PWM0A_OUT 25   //Set GPIO 25 as PWM0A
#define GPIO_PWM1A_OUT 26   //Set GPIO 26 as PWM1A
#define GPIO_PWM2A_OUT 27   //Set GPIO 27 as PWM2A

//#######_DRV8305_########
#define enGate 17       //Chip Enable
#define nFault 14       //Fault reading
#define so1 36          //Pins connected to DRV's current sensors, one for each phase
#define so2 35
#define so3 34
int a1, a2, a3;         //Current readings from internal current sensor amplifiers

//#######_MA730_########
//A and B encoder inputs
#define arduinoInt1 4             // interrupt 0
#define arduinoInt2 2             // interrupt 1

//#####_TEMPERATURE_#####
#define vTemp 39
float vOut, temp;
bool tFlag = false;

//########_BLDC Motor_########
//  BLDCMotor( int phA, int phB, int phC, int pp, int en)
//  - phA, phB, phC - motor A,B,C phase pwm pins
//  - pp            - pole pair number
//  - enable pin    - (optional input)
//  - Calibration power percentage
BLDCMotor motor = BLDCMotor(25, 26, 27, 7, 0.3);

//  Encoder(int encA, int encB , int cpr, int index)
//  - encA, encB    - encoder A and B pins
//  - ppr           - impulses per rotation  (cpr=ppr*4)
//  - index pin     - (optional input)
Encoder encoder = Encoder(arduinoInt1, arduinoInt2, 1024);
// interrupt ruotine intialisation
void doA1(){encoder.handleA();}
void doB1(){encoder.handleB();}

//#####_SPI_#######
#define cs 5      //Chip-select

//#####_System Gains_#####
float ki = 0.025;
float ti = 1.0;
float lpFilter = 0.000;
float kp = 15;
float voltageRamp = 100;
float voltageLimit = 1.4/2;
float velocityLimit = 2000;

//Time managing variables
float runTime, prevT = 0, timeDif, stateT, stateT2;
int timeInterval = 1000;

//Target variable
float target = 0;
// loop stats variables
unsigned long t = 0;
long timestamp = micros();

static void IRAM_ATTR setup_MCPWM();

void setup() {
  //Serial communication to virtual COM
  Serial.begin(115200);
  setup_MCPWM();
  _delay(350);

  //  Quadrature::ENABLE - CPR = 4xPPR  - default
  //  Quadrature::DISABLE - CPR = PPR
  encoder.quadrature = Quadrature::ENABLE;
  // check if you need internal pullups
  // Pullup::EXTERN - external pullup added - dafault
  // Pullup::INTERN - needs internal arduino pullup
  encoder.pullup = Pullup::EXTERN;
  // initialise encoder hardware
  encoder.init();
  encoder.enableInterrupts(doA1,doB1);

  //Pin modes for every pin
  pinMode(vTemp, INPUT);
  pinMode(enGate, OUTPUT);
  digitalWrite(enGate, LOW);
  pinMode(nFault, INPUT);
  pinMode(so1, INPUT);
  pinMode(so2, INPUT);
  pinMode(so3, INPUT);

  //SPI start up
  pinMode(cs, OUTPUT);
  digitalWrite(cs, HIGH);
  SPI.begin();
  SPI.setBitOrder(MSBFIRST);
  SPI.setDataMode(SPI_MODE1);
  //Serial.println(MOSI);
  //Serial.println(MISO);
  //Serial.println(SCK);

  //Motor driver initialization
  delay(500);
  Serial.println("DRV8305 INIT");
  drv_init();
  delay(500);

  Serial.println("enGate Enabled");
  digitalWrite(enGate, HIGH);
  delay(500);

  //BLDC motor initialization
  motor.voltage_power_supply = 12;

  // set FOC loop to be used: ControlType::voltage, velocity, angle
  motor.controller = ControlType::angle;
  
  // velocity PI controller parameters, default K=0.5 Ti = 0.01
  motor.PI_velocity.P = ki;
  motor.PI_velocity.I = ti;
  motor.PI_velocity.voltage_limit = voltageLimit;
  motor.PI_velocity.voltage_ramp = voltageRamp;
  motor.LPF_velocity.Tf = lpFilter;
  
  // angle P controller, default K=70
  motor.P_angle.P = kp;
  // maximal velocity of the poisiiton control, default 20
  motor.P_angle.velocity_limit = velocityLimit;
  
  // link the motor to the sensor
  motor.linkSensor(&encoder);
  // intialise motor
  motor.init();
  // align encoder and start FOC
  motor.initFOC();
  Serial.println("Ready BLDC.");
  _delay(1000);
  printGains();

  //analogSetSamples(2);
}


void loop() {
  motor.loopFOC();
  serialEvent();

  runTime = micros();
  timeDif = runTime - prevT;
  prevT = runTime;
  stateT += timeDif;
  stateT2 += timeDif;

  if(stateT >= 1000){
    motor.move(target);
    stateT = 0;
    //Serial.println(sp);
  }
  
  //Read voltage from temperature sensor and transform it to °C
  vOut = analogRead(vTemp);
  temp = ((vOut*(3.3)/4095)-0.4)/0.0195;
  if (temp >= 75 && tFlag == false){
    digitalWrite(enGate, LOW);
    tFlag = true;
    Serial.print("enGate Disabled - Temperature protection: ");
    Serial.println(temp);
  }
  else if (tFlag == true && temp <= 75){
    digitalWrite(enGate, HIGH);
    tFlag = false;
    Serial.println("enGate Enabled - Temperature low");
  }
  //Serial.println(temp);

  //Read nFault pin from DRV8305 - LOW == error / HIGH == normal operation
  int fault = digitalRead(nFault);
  //Serial.println(fault);

  //Read voltages from the DRV8305 current sensors and sense resistors
  
  if(stateT2 >= 2000){
     a1 = analogRead(so1);
     a2 = analogRead(so2);
     a3 = analogRead(so3);
     stateT2 = 0;
  }


  Serial.print(a1);
  Serial.print(",");
  Serial.print(a2);
  Serial.print(",");
  Serial.println(a3);
}

//Set DRV8305 to three PWM inputs mode
void drv_init(){
  digitalWrite(cs, LOW);
  int resp = SPI.transfer(B00111010);
  int resp2 = SPI.transfer(B10000110);
  digitalWrite(cs, HIGH);
  //010 10010110
  //010 00000110
  Serial.println(resp);
  Serial.println(resp2);
  
  digitalWrite(cs, LOW);
  int resp3 = SPI.transfer(B01010111);
  int resp4 = SPI.transfer(B00000000);
  digitalWrite(cs, HIGH);
  Serial.println(resp3);
  Serial.println(resp4);
  
  digitalWrite(cs, LOW);
  int resp5 = SPI.transfer(B01010000);
  int resp6 = SPI.transfer(B00000000);
  digitalWrite(cs, HIGH);
}
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

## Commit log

2020-05-27 Main Arduino code
2020-06-07 Added images and schematics
    [Gerber_BoardOutline.GKO, Gerber_BottomLayer.GBL, Gerber_BottomSilkLayer.GBO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]
2020-07-01 BOM added
    [BOM_JC20.01.csv]
2020-07-01 Created CAD folder
    [6.ESP-32.SLDPRT, ESP-WROOM-32.sldprt, ESP32_DevKit1.SLDASM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]
2020-07-01 Updated README: added Burshless Motor Selection section
2020-07-01 Added more CAD parts
    [Diametrical Magnet 6x6mm.SLDPRT, Magnet Joint 012.SLDPRT, PCB Janus Controller 20.01.SLDPRT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]
2020-07-01 Updated README: added The three-phase gate driver section
2020-07-02 Added through hole BOM
    [BOM_JC20.01.csv, BOM_SMD_JC20.01.csv, BOM_through_hole_JC20.01.csv]
2020-07-07 Added .STL parts
    [6.ESP-32.STL, Diametrical Magnet 6x6mm.STL, ESP-WROOM-32.STL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]
2020-07-23 Updated README: Added encoder example code section
2020-07-23 Added Encoder Tester
2020-08-11 Controller Version 20.02
    [6.ESP-32.SLDPRT, 6.ESP-32.STL, BOM_SMD_JC20.01.csv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]
2020-08-11 Clean repo
    [6.ESP-32.SLDPRT, 6.ESP-32.STL, Diametrical Magnet 6x6mm.SLDPRT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]
2020-08-11 Cleaning repo
    [BOM_SMD_JC20.01.csv, BOM_through_hole_JC20.01.csv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]
2020-08-11 Updated Gerber
    [Gerber_BoardOutline.GKO, Gerber_BottomLayer.GBL, Gerber_BottomSilkLayer.GBO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]
